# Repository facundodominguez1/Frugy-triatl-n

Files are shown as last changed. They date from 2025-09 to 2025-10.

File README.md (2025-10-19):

# Robot Triatlon "FRUGY" - Bonaerenses 2025

Imagen de WhatsApp 2025-10-18 a las 21 52 04_16612dd6

Imagen de WhatsApp 2025-10-18 a las 21 53 57_ca518bda

## Frugy 

Este proyecto robot triatlón fue creado con la intencion de competir en las Bonaerenses 21/08/2025. Que fue llevado por los alumnos de 5°6 Ulises Basabe, Facundo Dominguez, Gonzalo Flores y Ramiro Trejo. A lo largo de varias pruebas realizadas por los mismos.

**Todo este proyecto pudo funcionar gracias a los programas de Arduino Ide para su desarollo de software, KiCad 9.0 para su desarrollo de PCBs, y por ultimo Fusion 360 para su diseño 3D**

## SUMO RC
Esta categoría llamada Sumo RC (Radio Controlado), se basa en quitar del tatami al rival, el cual una persona está encargada de maniobrar al robot.

## VELOCISTA
Por este lado el robot tiene como objetivo completar una pista de carreas de la manera mas rápida y precisa posible, que en esta pista se pueden llegar a incluir obstaculos para dificultar la vuelta

## DESPEJA AREA
Esta rama es cuando el robot tiene que sacar una serie de cubos de una pista de la manera mas eficiente, obteniendo así dsitintos puntajes sin este poder salir de la misma 

## ⚒ LISTA DE COMPONENTES

- 2 Baterias de LiPo 3s 1050 mAh
- 5 Sensores de distancia AD32
- 1 Regleta de sensores QTR8A
- 3 Sensores de piso TCRT5000
- 2 Motores JGA25-370 DE 280RPM
- 2 Drivers TA6586
- 1 Microcontrolador ESP32 de 38 Pines
- 2 Placas de pertinax 10cmX10cm
- 1 Led Neopixel

## FALLAS Y DETALLES 

- En este proyecto hubo muchos problemas con calculo de tiempos
- Desconocimiento para un proyecto tan importante
- No tener muy en cuenta el gasto total del proyecto

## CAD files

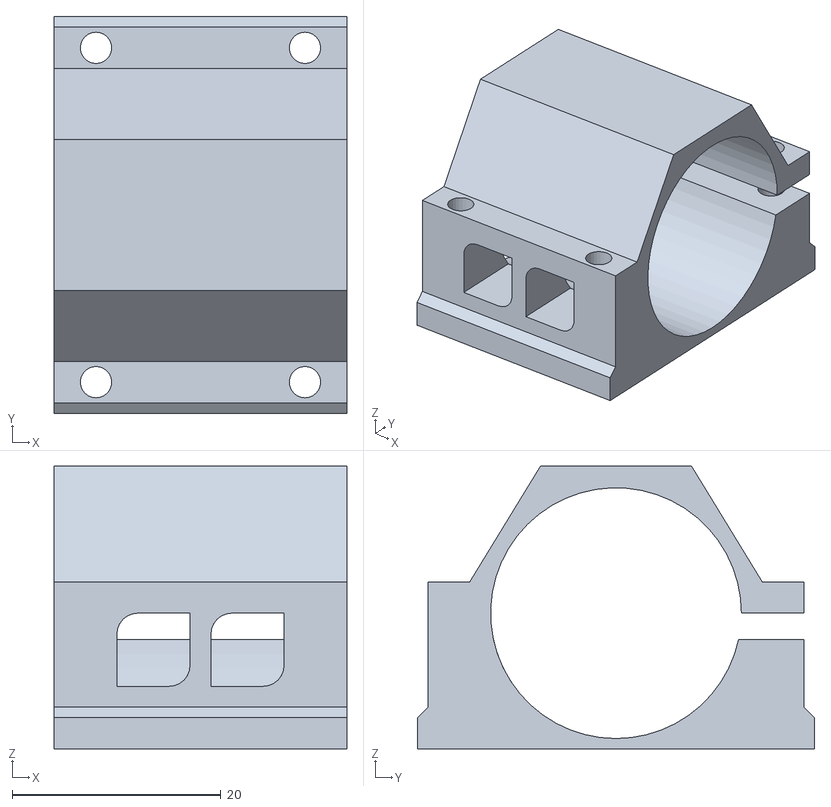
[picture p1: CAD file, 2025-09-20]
Diseño 3D/Piezas 3d stl y gcode/Braket.stl
28.0 x 38.0 x 27.1

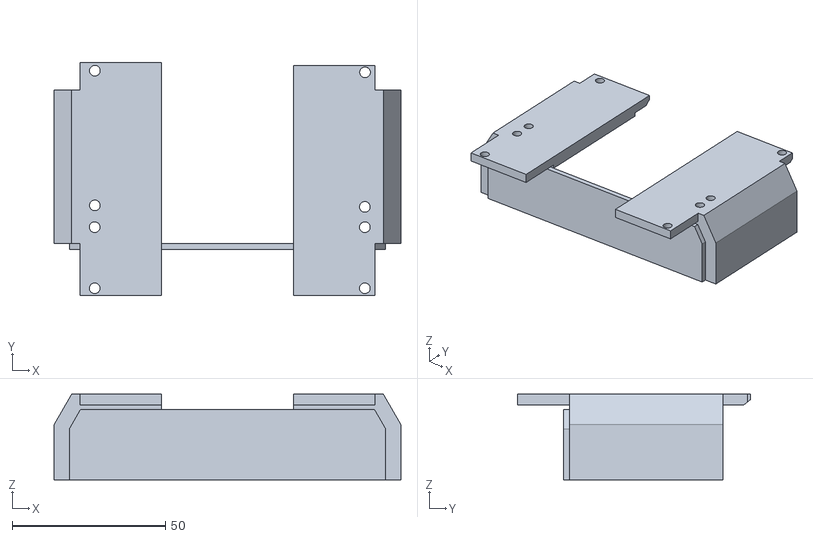
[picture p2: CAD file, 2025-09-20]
Diseño 3D/Piezas 3d stl y gcode/Soporte de placa.stl
113.0 x 76.0 x 28.0

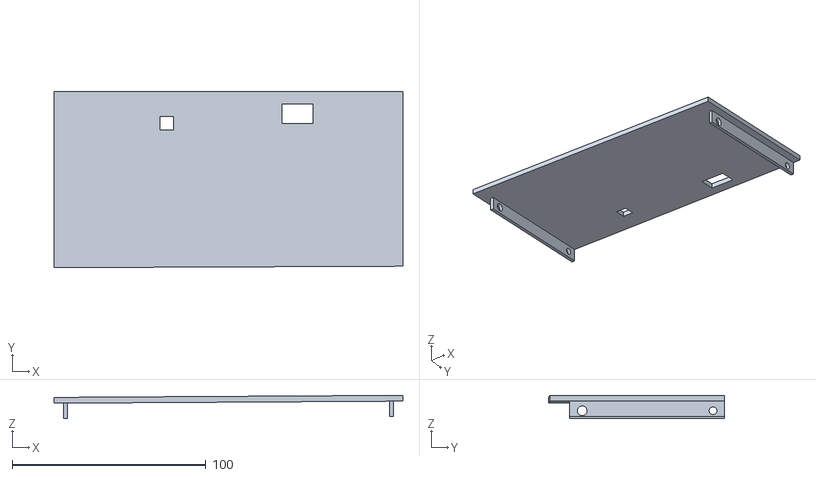
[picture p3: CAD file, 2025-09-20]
Diseño 3D/Piezas 3d stl y gcode/techo.stl
180.0 x 90.9 x 12.0

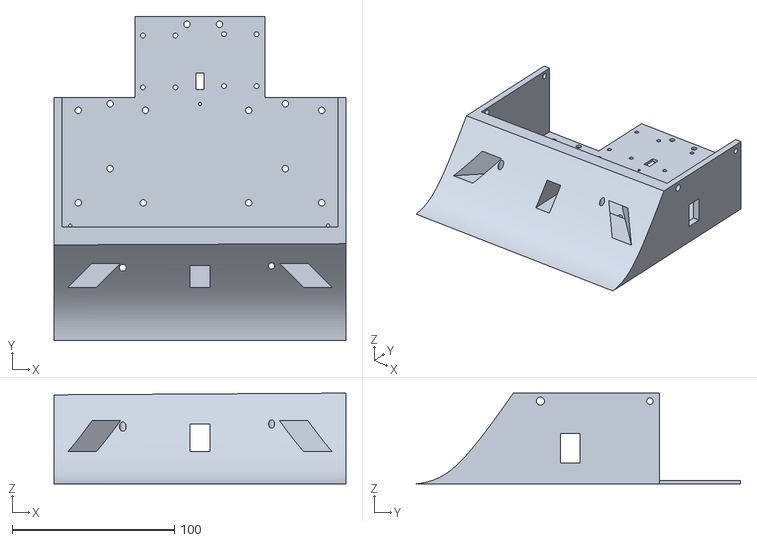
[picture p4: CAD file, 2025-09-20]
Diseño 3D/Piezas 3d stl y gcode/carroserìa Frugy.stl
180.0 x 200.0 x 56.0

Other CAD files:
Diseño 3D/Frugy.f3z

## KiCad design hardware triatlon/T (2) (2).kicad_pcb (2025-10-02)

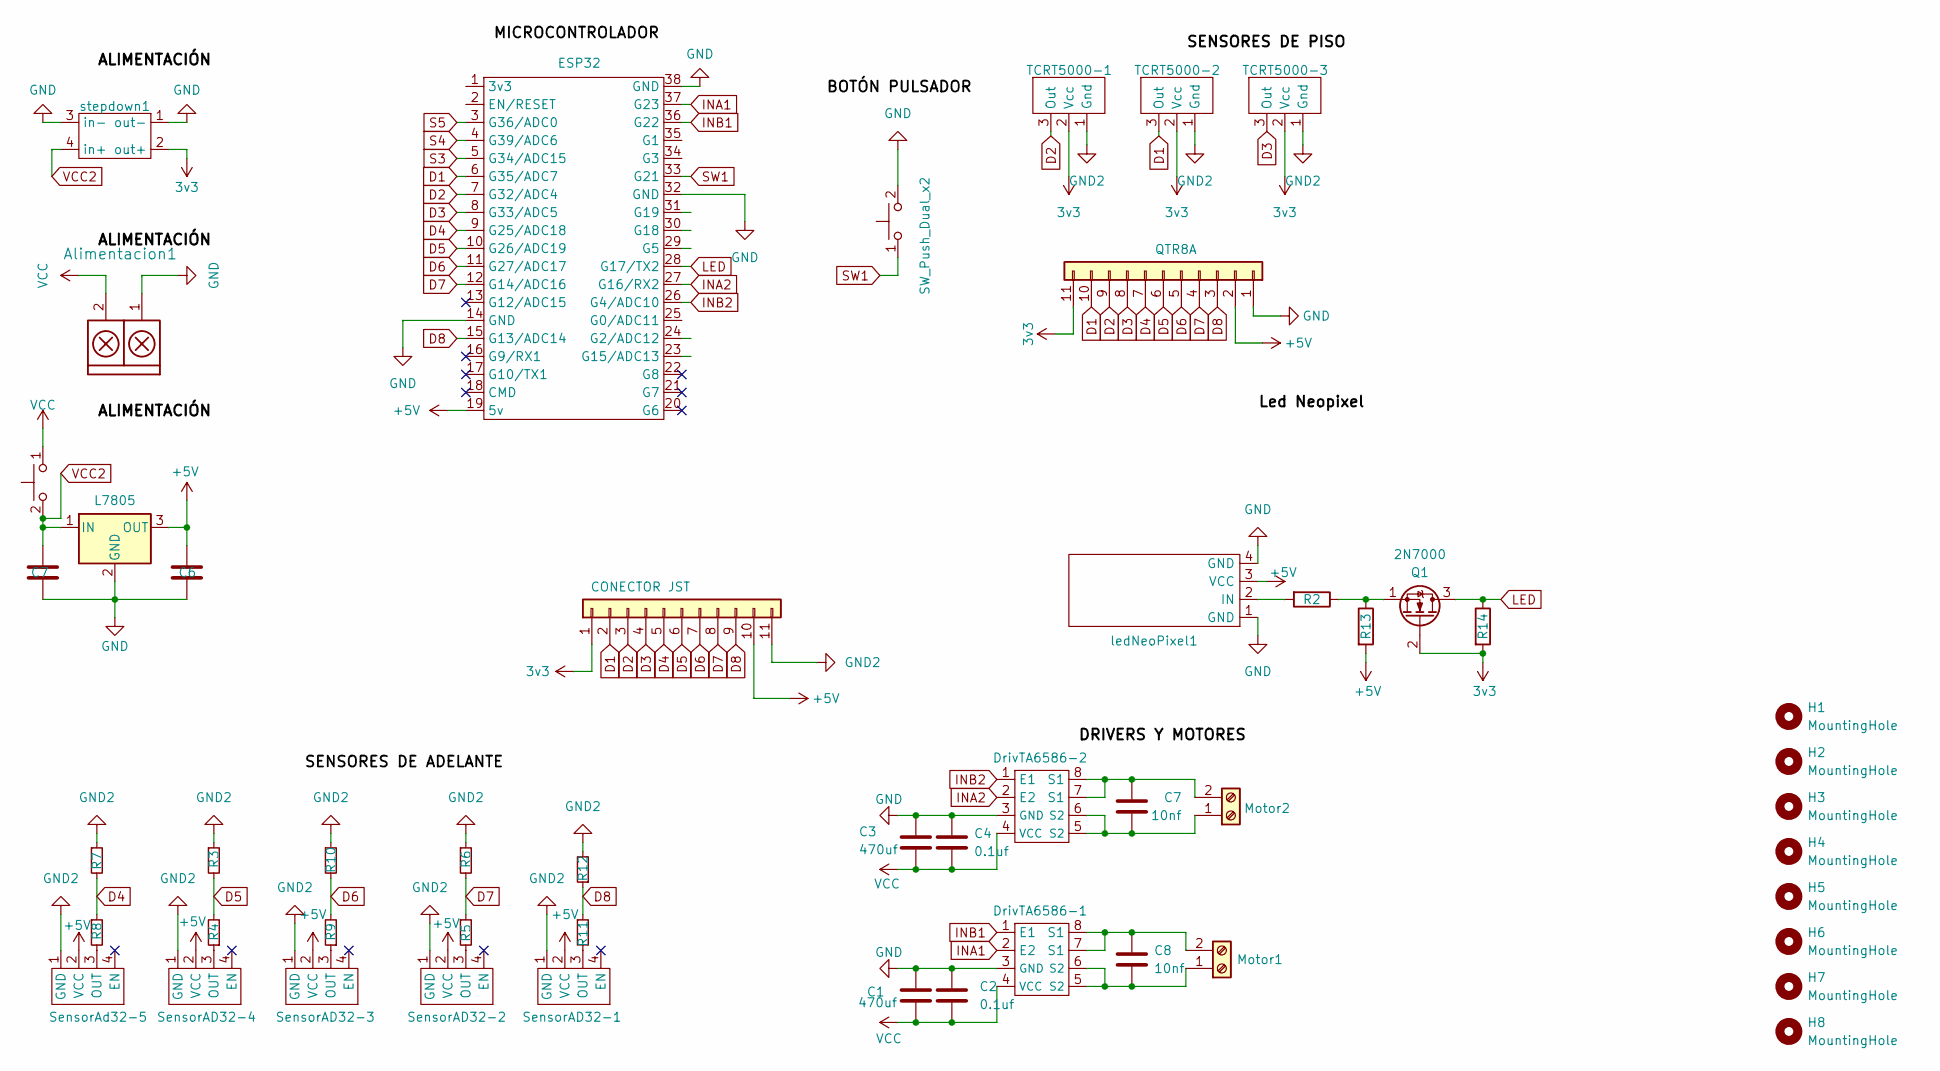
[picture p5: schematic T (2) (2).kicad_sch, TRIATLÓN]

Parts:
Alimentacion1: TB_1X2; BORNERA2_AZUL
C1, C3: 470uf; CP_Radial_D8.0mm_P3.80mm
C2, C4: 0.1uf; C_Disc_D5.0mm_W2.5mm_P2.50mm
C5: C7; C_Disc_D5.0mm_W2.5mm_P2.50mm
C6: 0.01uf; C_Disc_D5.0mm_W2.5mm_P2.50mm
C7, C8: 10nf; C_Disc_D5.0mm_W2.5mm_P2.50mm
DrivTA6586-1, DrivTA6586-2: DIP-8_W7.62mm
ESP32: ESP32_T
H1, H2, H3, H4, H5, H6, H7, H8: MountingHole; MountingHole_3.2mm_M3_DIN965
J2: QTR8A; JST_EH_B11B-EH-A_1x11_P2.50mm_Vertical
J3: CONECTOR JST; JST_EH_B11B-EH-A_1x11_P2.50mm_Vertical
Motor1, Motor2: Screw_Terminal_01x02; BORNERA2_AZUL
Q1: 2N7000; TO-92_Wide
R2: 330; R_Axial_DIN0207_L6.3mm_D2.5mm_P7.62mm_Horizontal
R3, R6, R7, R10, R12: 2.2K; R_Axial_DIN0207_L6.3mm_D2.5mm_P7.62mm_Horizontal
R4, R5, R8, R9, R11: 1K; R_Axial_DIN0207_L6.3mm_D2.5mm_P7.62mm_Horizontal
R13, R14: 10K; R_Axial_DIN0207_L6.3mm_D2.5mm_P7.62mm_Horizontal
SensorAD32-1, SensorAD32-2, SensorAD32-3, SensorAD32-4: JST-4V
SensorAd32-5: JST-4V
TCRT5000-1, TCRT5000-2, TCRT5000-3: JST-3V
U10: L7805; TO-220-3_Vertical
boton1: SW_Push_Dual_x2; PinHeader_1x02_P2.54mm_Vertical
boton3: SW_Push_Dual_x2; BORNERA3_AZUL
ledNeoPixel1: PinHeader_1x04_P2.54mm_Vertical
stepdown1: STEPDOWN

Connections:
3v3: J2.11, J3.1, Q1.2 (G), R14.2, TCRT5000-1.2 (Vcc), TCRT5000-2.2 (Vcc), TCRT5000-3.2 (Vcc), stepdown1.2 (out+)
+5V: C6.1, ESP32.19 (5v), J2.2, J3.10, R13.2, SensorAD32-1.2 (VCC), SensorAD32-2.2 (VCC), SensorAD32-3.2 (VCC), SensorAD32-4.2 (VCC), SensorAd32-5.2 (VCC), U10.3 (OUT), ledNeoPixel1.3 (VCC)
D1: ESP32.6 (G35/ADC7), J2.10, J3.2, TCRT5000-2.3 (Out)
D2: ESP32.7 (G32/ADC4), J2.9, J3.3, TCRT5000-1.3 (Out)
D3: ESP32.8 (G33/ADC5), J2.8, J3.4, TCRT5000-3.3 (Out)
D4: ESP32.9 (G25/ADC18), J2.7, J3.5, R7.2, R8.1
D5: ESP32.10 (G26/ADC19), J2.6, J3.6, R3.2, R4.2
D6: ESP32.11 (G27/ADC17), J2.5, J3.7, R9.2, R10.2
D7: ESP32.12 (G14/ADC16), J2.4, J3.8, R5.1, R6.2
D8: ESP32.15 (G13/ADC14), J2.3, J3.9, R11.1, R12.1
GND: Alimentacion1.1, C1.1, C2.1, C3.1, C4.1, C5.2, C6.2, DrivTA6586-1.3 (GND), DrivTA6586-2.3 (GND), ESP32.14 (GND), ESP32.32 (GND), ESP32.38 (GND), J2.1, U10.2 (GND), boton1.2 (D), ledNeoPixel1.1 (GND), ledNeoPixel1.4 (GND), stepdown1.1 (out-), stepdown1.3 (in-)
GND2: J3.11, R3.1, R6.1, R7.1, R10.1, R12.2, SensorAD32-1.1 (GND), SensorAD32-2.1 (GND), SensorAD32-3.1 (GND), SensorAD32-4.1 (GND), SensorAd32-5.1 (GND), TCRT5000-1.1 (Gnd), TCRT5000-2.1 (Gnd), TCRT5000-3.1 (Gnd)
INA1: DrivTA6586-1.2 (E2), ESP32.37 (G23)
INA2: DrivTA6586-2.2 (E2), ESP32.27 (G16/RX2)
INB1: DrivTA6586-1.1 (E1), ESP32.36 (G22)
INB2: DrivTA6586-2.1 (E1), ESP32.26 (G4/ADC10)
LED: ESP32.28 (G17/TX2), Q1.3 (D), R14.1
unnamed: C8.2, DrivTA6586-1.5 (S2), DrivTA6586-1.6 (S2), Motor1.1
unnamed: C8.1, DrivTA6586-1.7 (S1), DrivTA6586-1.8 (S1), Motor1.2
unnamed: C7.2, DrivTA6586-2.5 (S2), DrivTA6586-2.6 (S2), Motor2.1
unnamed: C7.1, DrivTA6586-2.7 (S1), DrivTA6586-2.8 (S1), Motor2.2
unnamed: Q1.1 (S), R2.1, R13.1
unnamed: R11.2, SensorAD32-1.3 (OUT)
unnamed: R5.2, SensorAD32-2.3 (OUT)
unnamed: R9.1, SensorAD32-3.3 (OUT)
unnamed: R4.1, SensorAD32-4.3 (OUT)
unnamed: R8.2, SensorAd32-5.3 (OUT)
unnamed: R2.2, ledNeoPixel1.2 (IN)
S3: ESP32.5 (G34/ADC15)
S4: ESP32.4 (G39/ADC6)
S5: ESP32.3 (G36/ADC0)
SW1: ESP32.33 (G21), boton1.1 (C)
VCC: Alimentacion1.2, C1.2, C2.2, C3.2, C4.2, DrivTA6586-1.4 (VCC), DrivTA6586-2.4 (VCC), boton3.1 (C)
VCC2: C5.1, U10.1 (IN), boton3.2 (D), stepdown1.4 (in+)

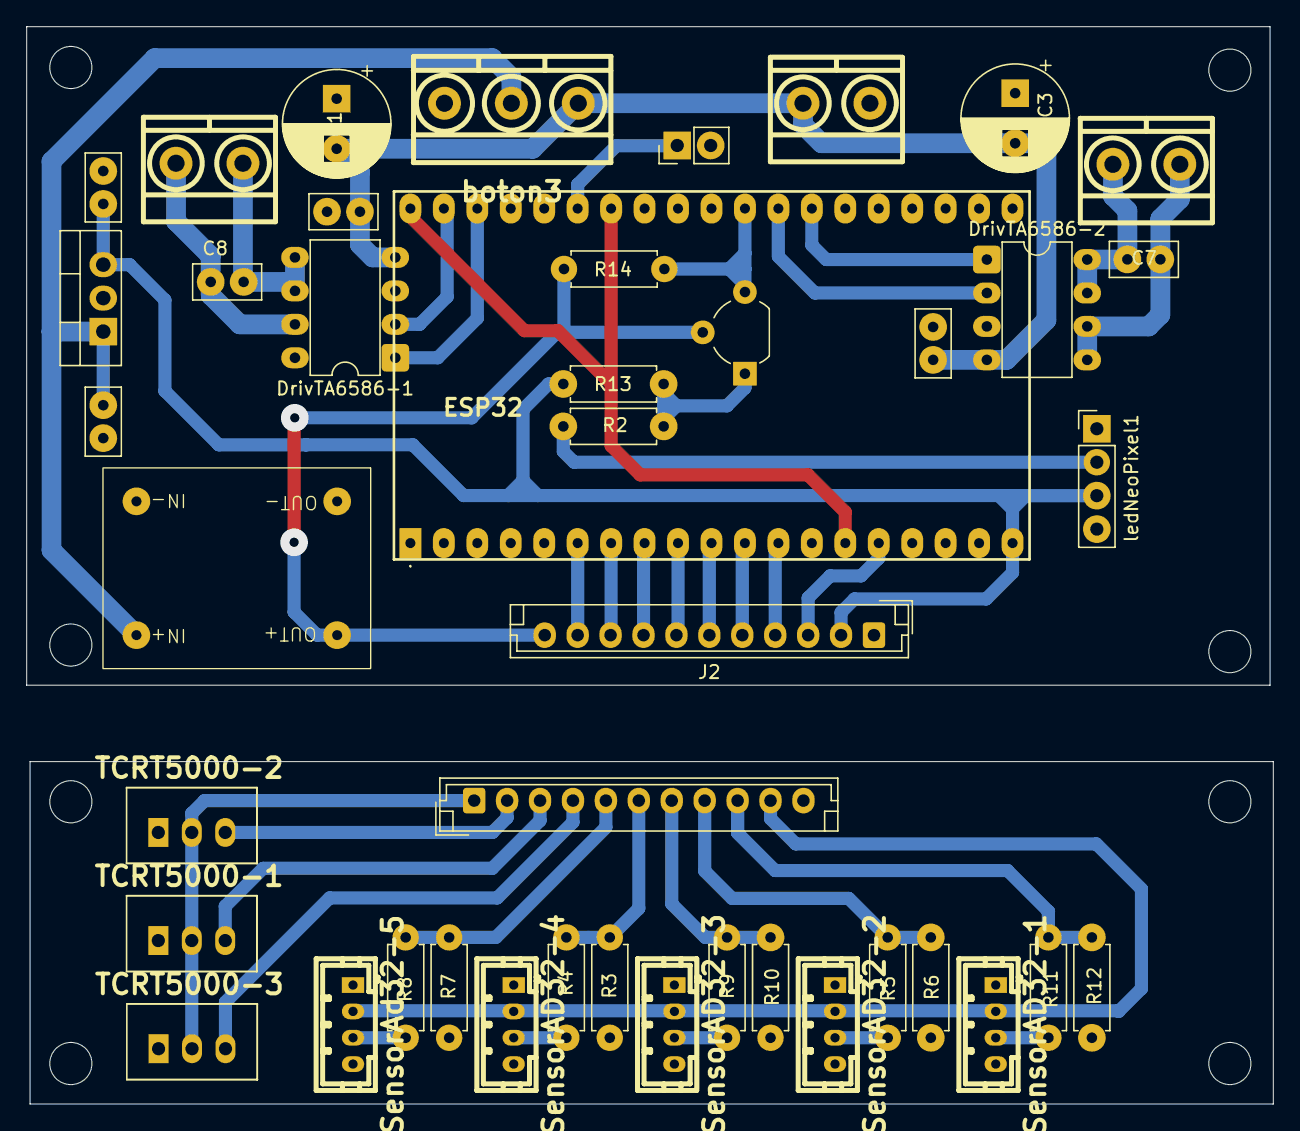
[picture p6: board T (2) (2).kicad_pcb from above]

Board: 2 copper layers, 94.7 x 81.8 mm, 51 parts (0 on the bottom side), 31 nets.

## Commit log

2025-09-13 soporte motores
2025-09-20 Archivo Fusión 360
    [carroserìa Frugy.f3z]
2025-09-20 Carrocería Frugy stl
2025-09-20 Carrocería archivo Fusión 360
    [Frugy.f3z]
2025-09-20 Archivos stl
    [Braket.stl, Soporte de placa.stl, carroserìa Frugy.stl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]
2025-10-02 Add files via upload
    esta placa fue la unica que se usó y que nos dio un fallo de que se quemo la placa
    [T (2) (2).kicad_pcb, T (2) (2).kicad_sch]
